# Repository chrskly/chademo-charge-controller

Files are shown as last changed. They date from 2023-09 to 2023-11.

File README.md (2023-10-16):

# CHAdeMO Implementation

This repo contains a car-side implementation of the CHAdeMO EV charging
standard including both the hardware and firmware.

## Features

* Supports CHAdeMO protocols v0.9, v1.0, and v2.0.
* Automatic sleep, wake on plug insertion.
* Separate manual wake button option.

## Chademo Plug Pinout

 1. Ground
 2. CP : evse => car, IN1, contactor +ve signal, goes high when active, sensed by 'f'
 3. nc
 4. CP3 : car => evse, OUT1, charge enable, sensed by 'k'
 5. HV-
 6. HV+
 7. CS : connection check, goes low when plug inserted, sensed by 'h'
 8. CAN H
 9. CAN L
10. CP2 : evse => car, IN2, contactor -ve signal, goes low when active, sensed by 'g'

OUT2, contactor override, pull low to allow CP2 signal through

## Charging start sequence

1. Car pulls CP high (12V) through R3 (1kΩ) when plug is inserted
2. User presses start button on station
3. Station pulls CP high (IN1), d1 closes, +ve contactor closes
4. Car and station start sending CAN messages
5. Car and station check each others params for compatability
6. Car pulls CP3 low and sets CAN vehicleChargingEnabled flag to true to
   indicate it is ready to go ahead with charging
7. Station locks plug to vehicle
8. Station performs insulation test
9. Station pulls CP2 low (IN2), d2 closes, -v3 contactor closes
10. Car ramps up current request. Energy transfer begins.

## Charging stop sequence

1. Car stops pulling CP3 low and sets CAN vehicleChargingEnabled to false.
2. Station deactivates CP and CP2
3. Station unlocks plug

## Questions

- [ ] When to use vehicleChargingEnabled and when to use vehicleRequestingStop?

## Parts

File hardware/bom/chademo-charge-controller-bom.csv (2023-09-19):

Comment | Designator | Footprint | LCSC
TPS62160DGKR | IC1 | MSOP-8 | C60726
SS54 | D1 | SMB(DO-214AA) | C880743
10uF | C1,C5,C6,C7, | 0805_C | C15850
2.2uH | L1 | IND-SMD | C92941
100kΩ | R1 | 0805_R | C149504
220kΩ | R2 | 0805_R | C17539
47kΩ | R3 | 0805_R | C17713
22uF | C4 | 0805_C | C2835558
0.1uF | C2,C3 | 0805_C | C49678
MCP2515-I/ST | IC2,IC4 | TSSOP-20 | C15193
SN65HVD230 | IC3,IC5 | SOIC-8 | C12084
120Ω | R12,R13 | 0805_R | C17437
560Ω | R17,R18,R19 | 0805_R | C28636
10Ω | R5,R8,R9,R11,R15,R20,R23 | 0805_R | C17415
1.6kΩ | R4,R10,R16,R21 | 0805_R | C2930156
led | D2,D3,D4,D5,D6,D7,D8 | 0805 | C434432
200Ω | R6 | 0805_R | C17540
1kΩ | R14 | 0805_R | C17513
100Ω | R7,R22 | 0805_R | C17408
PC817 | U2,U3,U4,U5,U6,U7 | DIP-4 | C3025067
NCV8402ASTT1G | IC6 | SOT223 | C77755

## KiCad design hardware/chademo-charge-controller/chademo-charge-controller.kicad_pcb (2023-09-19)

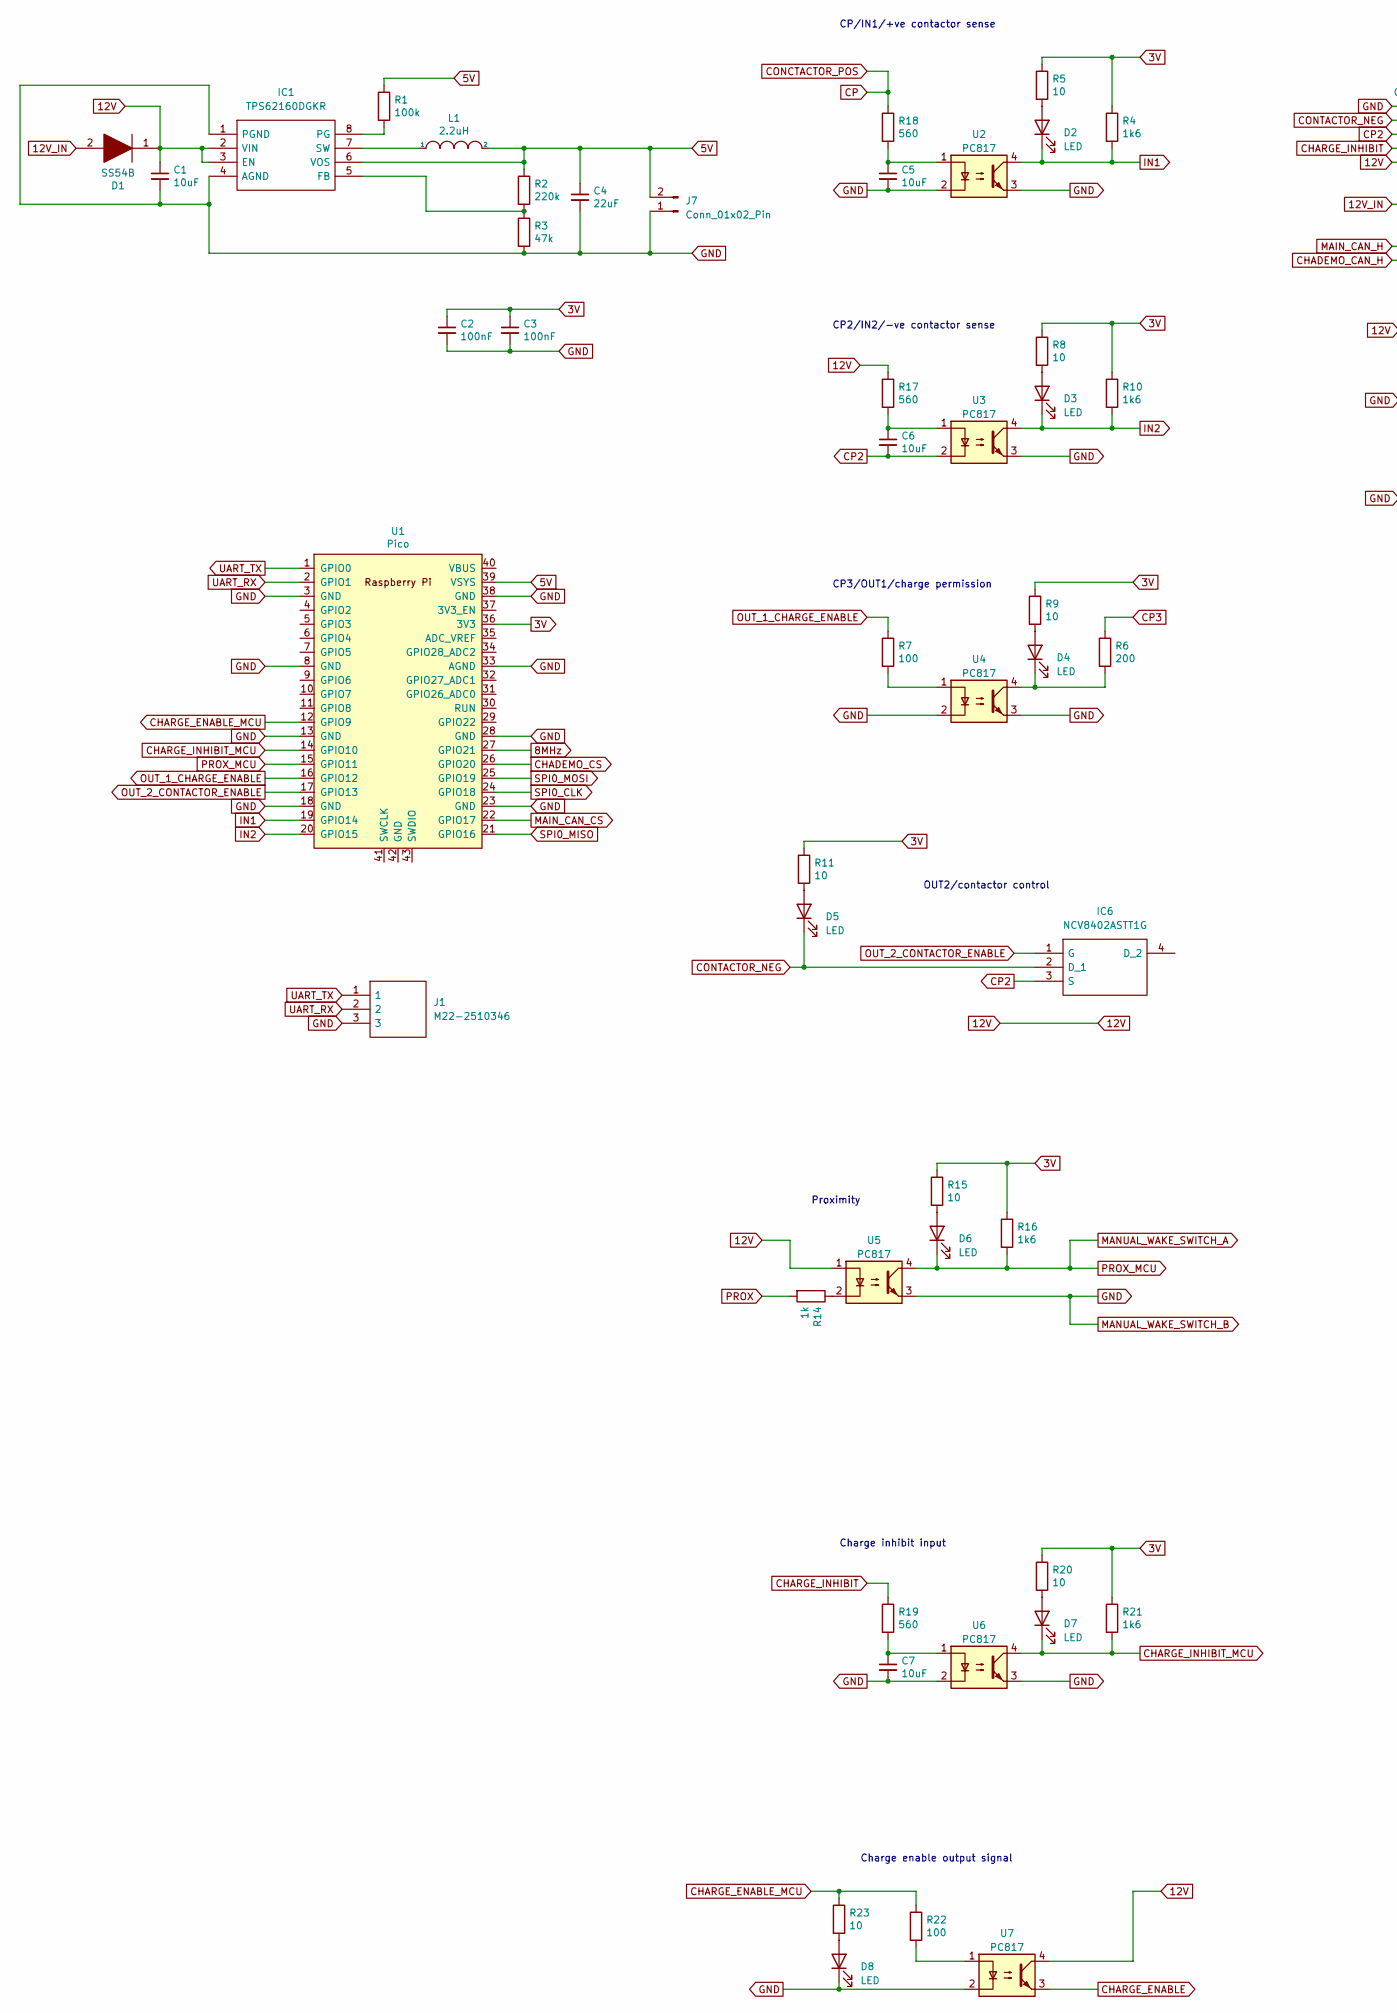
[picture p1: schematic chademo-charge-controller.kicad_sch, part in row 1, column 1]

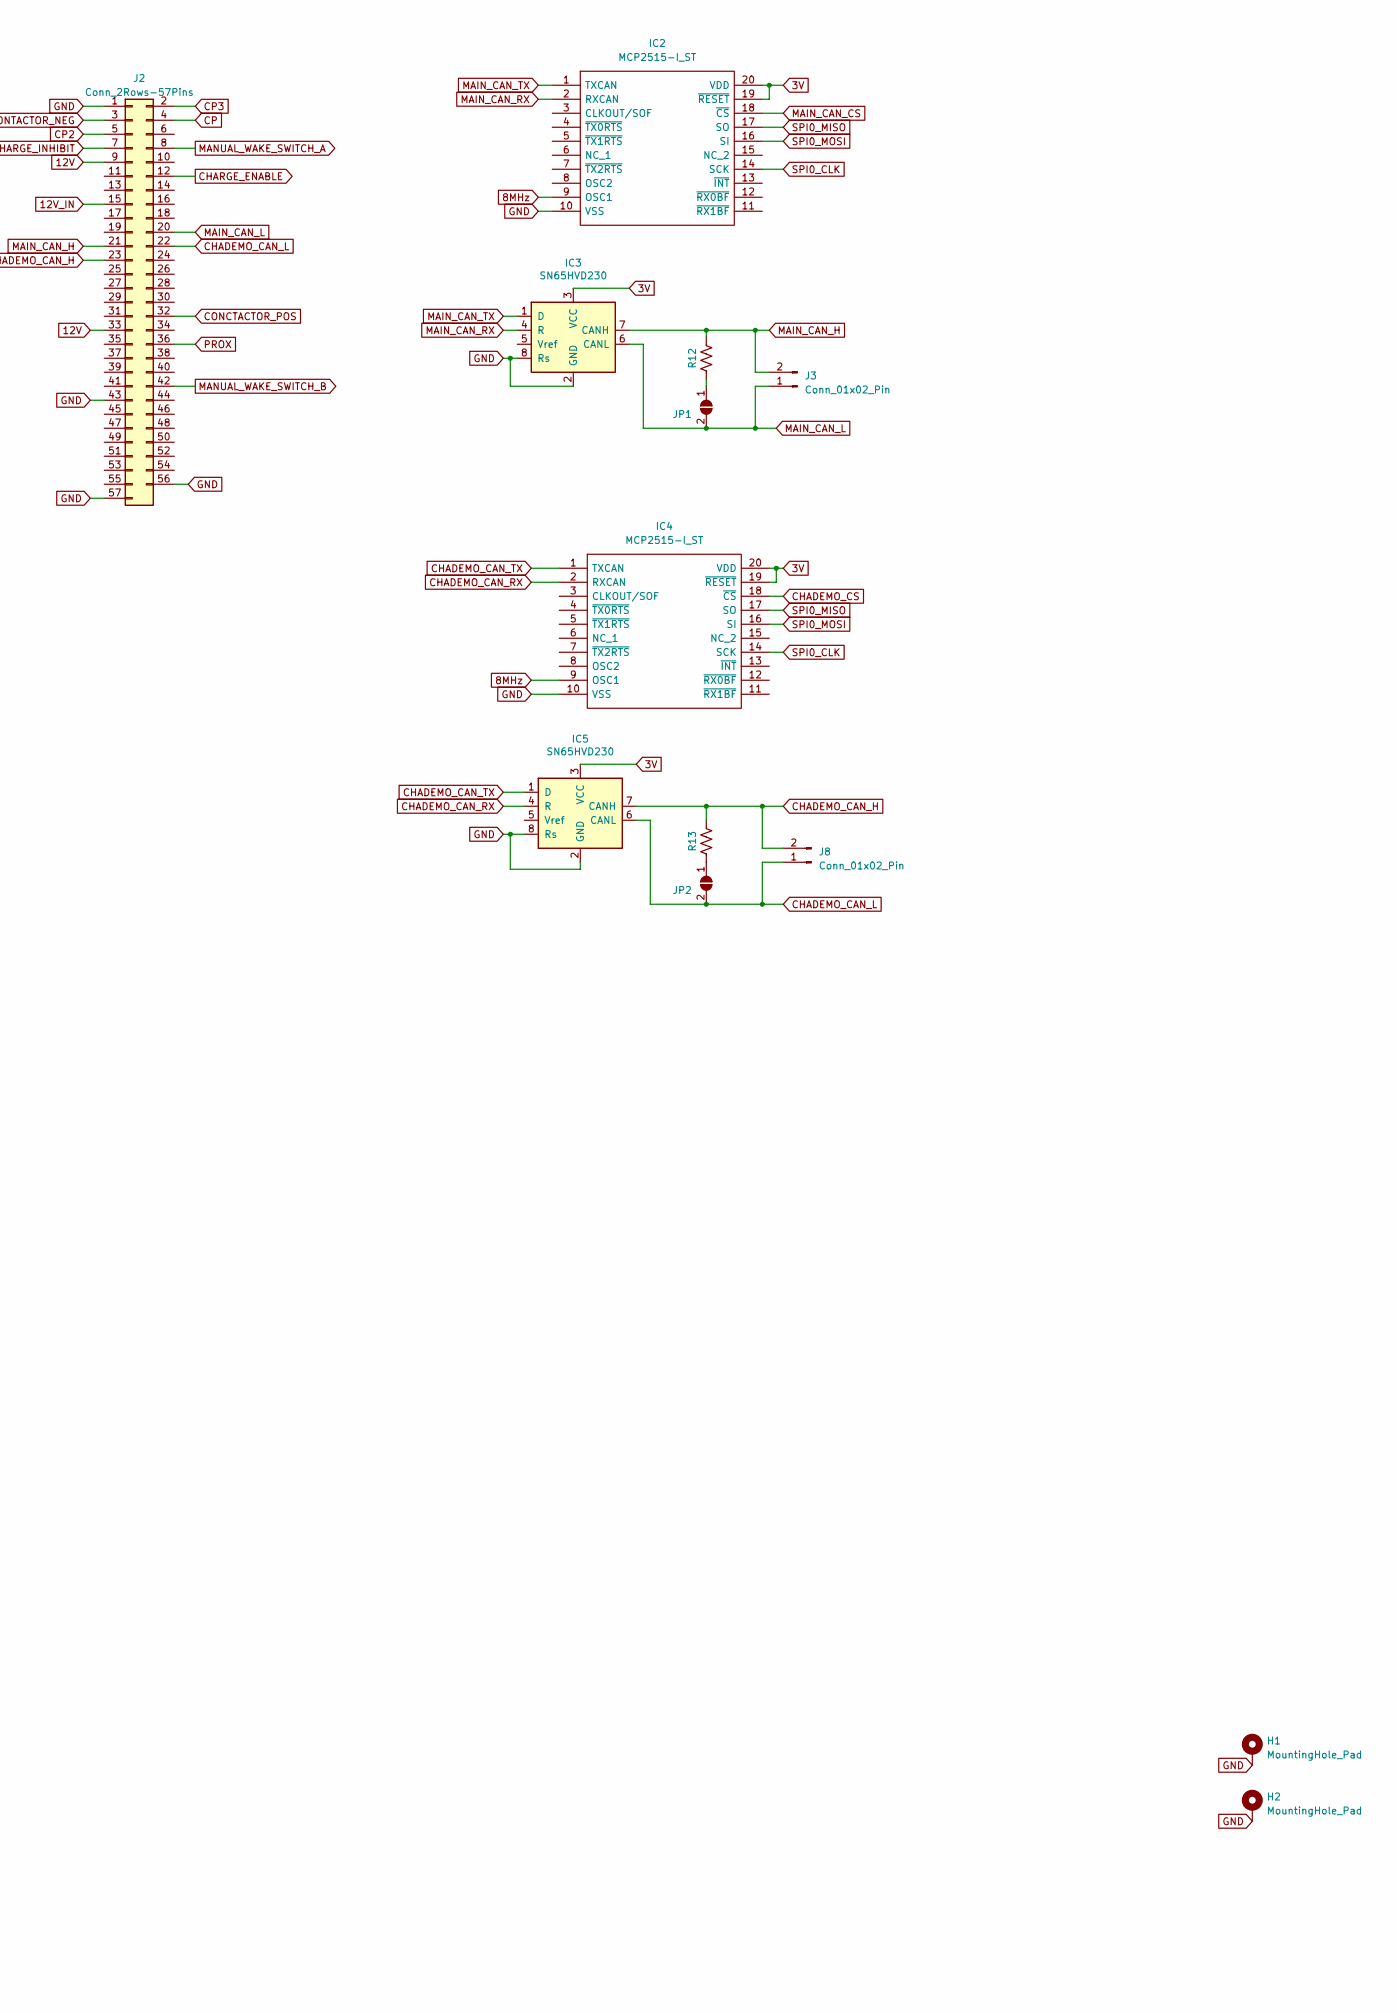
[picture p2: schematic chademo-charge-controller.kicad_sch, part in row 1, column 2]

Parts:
C1, C5, C6, C7: 10uF; C_0603_1608Metric
C2, C3: 100nF; C_0603_1608Metric
C4: 22uF; C_0805_2012Metric
D1: SS54B; DIOM5336X244N; Manufacturer_Part_Number SS54B
D2, D3, D4, D5, D6, D7, D8: LED; LED_0805_2012Metric
H1, H2: MountingHole_Pad; MountingHole_3.2mm_M3_DIN965_Pad
IC1: TPS62160DGKR; SOP65P490X110-8N; Manufacturer_Part_Number TPS62160DGKR; Mouser Part Number 595-TPS62160DGKR
IC2, IC4: MCP2515-I_ST; SOP65P640X120-20N; Manufacturer_Part_Number MCP2515-I/ST
IC3, IC5: SN65HVD230; SOIC-8_3.9x4.9mm_P1.27mm
IC6: NCV8402ASTT1G; SOT230P700X175-4N; Manufacturer_Part_Number NCV8402ASTT1G; Mouser Part Number 863-NCV8402ASTT1G
J1: M22-2510346; PinHeader_1x03_P2.54mm_Horizontal; Manufacturer_Part_Number M22-2510346; Mouser Part Number 855-M22-2510346
J2: Conn_2Rows-57Pins; delphi56
J3, J7, J8: Conn_01x02_Pin; PinHeader_1x02_P2.54mm_Vertical
JP1, JP2: SolderJumper_2_Open; SolderJumper-2_P1.3mm_Open_Pad1.0x1.5mm
L1: 2.2uH; NR6028T220M
R1: 100k; R_0805_2012Metric
R2: 220k; R_0805_2012Metric
R3: 47k; R_0805_2012Metric
R4, R10, R16, R21: 1k6; R_0805_2012Metric
R5, R8, R9, R11, R15, R20, R23: 10; R_0805_2012Metric
R6: 200; R_0805_2012Metric
R7, R22: 100; R_0805_2012Metric
R12, R13: 120; R_0805_2012Metric
R14: 1k; R_0805_2012Metric
R17, R18, R19: 560; R_0805_2012Metric
U1: Pico; RPi_Pico_SMD_TH
U2, U3, U4, U5, U6, U7: PC817; DIP-4_W7.62mm

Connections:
3V: C2.1, C3.1, IC2.19 (~RESET), IC2.20 (VDD), IC3.3 (VCC), IC4.19 (~RESET), IC4.20 (VDD), IC5.3 (VCC), R4.1, R5.1, R8.1, R9.1, R10.1, R11.1, R15.1, R16.1, R20.1, R21.1, U1.36 (3V3)
5V: C4.1, IC1.6 (VOS), J7.2, L1.2, R1.1, R2.1, U1.39 (VSYS)
8MHz: IC2.9 (OSC1), IC4.9 (OSC1), U1.27 (GPIO21)
12V: C1.1, D1.1, IC1.2 (VIN), IC1.3 (EN), J2.9, J2.33, R17.1, U5.1, U7.4
12V_IN: D1.2, J2.15
CHADEMO_CAN_H: IC5.7 (CANH), J2.23, J8.2, R13.1
CHADEMO_CAN_L: IC5.6 (CANL), J2.22, J8.1, JP2.2 (B)
CHADEMO_CAN_RX: IC4.2 (RXCAN), IC5.4 (R)
CHADEMO_CAN_TX: IC4.1 (TXCAN), IC5.1 (D)
CHADEMO_CS: IC4.18 (~CS), U1.26 (GPIO20)
CHARGE_ENABLE: J2.12, U7.3
CHARGE_ENABLE_MCU: R22.1, R23.1, U1.12 (GPIO9)
CHARGE_INHIBIT: J2.7, R19.1
CHARGE_INHIBIT_MCU: D7.1 (K), R21.2, U1.14 (GPIO10), U6.4
CONCTACTOR_POS: J2.4, J2.32, R18.1
CONTACTOR_NEG: D5.1 (K), IC6.2 (D_1), J2.3
CP2: C6.2, IC6.3 (S), J2.5, U3.2
CP3: J2.2, R6.1
GND: C1.2, C2.2, C3.2, C4.2, C5.2, C7.2, D8.1 (K), H1.1, H2.1, IC1.1 (PGND), IC1.4 (AGND), IC2.10 (VSS), IC3.2 (GND), IC3.8 (Rs), IC4.10 (VSS), IC5.2 (GND), IC5.8 (Rs), J1.3, J2.1, J2.42, J2.43, J2.56, J2.57, J7.1, R3.2, U1.3 (GND), U1.8 (GND), U1.13 (GND), U1.18 (GND), U1.23 (GND), U1.28 (GND), U1.33 (AGND), U1.38 (GND), U2.2, U2.3, U3.3, U4.2, U4.3, U5.3, U6.2, U6.3, U7.2
IN1: D2.1 (K), R4.2, U1.19 (GPIO14), U2.4
IN2: D3.1 (K), R10.2, U1.20 (GPIO15), U3.4
MAIN_CAN_CS: IC2.18 (~CS), U1.22 (GPIO17)
MAIN_CAN_H: IC3.7 (CANH), J2.21, J3.2, R12.1
MAIN_CAN_L: IC3.6 (CANL), J2.20, J3.1, JP1.2 (B)
MAIN_CAN_RX: IC2.2 (RXCAN), IC3.4 (R)
MAIN_CAN_TX: IC2.1 (TXCAN), IC3.1 (D)
MANUAL_WAKE_SWITCH_A: D6.1 (K), J2.8, R16.2, U1.15 (GPIO11), U5.4
unnamed: C5.1, R18.2, U2.1
unnamed: C6.1, R17.2, U3.1
unnamed: C7.1, R19.2, U6.1
unnamed: D2.2 (A), R5.2
unnamed: D3.2 (A), R8.2
unnamed: D4.2 (A), R9.2
unnamed: D4.1 (K), R6.2, U4.4
unnamed: D5.2 (A), R11.2
unnamed: D6.2 (A), R15.2
unnamed: D7.2 (A), R20.2
unnamed: D8.2 (A), R23.2
unnamed: IC1.5 (FB), R2.2, R3.1
unnamed: IC1.8 (PG), R1.2
unnamed: IC1.7 (SW), L1.1
unnamed: JP1.1 (A), R12.2
unnamed: JP2.1 (A), R13.2
unnamed: R7.2, U4.1
unnamed: R14.1, U5.2
unnamed: R22.2, U7.1
OUT_1_CHARGE_ENABLE: R7.1, U1.16 (GPIO12)
OUT_2_CONTACTOR_ENABLE: IC6.1 (G), U1.17 (GPIO13)
PROX: J2.36, R14.2
SPI0_CLK: IC2.14 (SCK), IC4.14 (SCK), U1.24 (GPIO18)
SPI0_MISO: IC2.17 (SO), IC4.17 (SO), U1.21 (GPIO16)
SPI0_MOSI: IC2.16 (SI), IC4.16 (SI), U1.25 (GPIO19)
UART_RX: J1.2, U1.2 (GPIO1)
UART_TX: J1.1, U1.1 (GPIO0)

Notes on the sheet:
CP/IN1/+ve contactor sense
OUT2/contactor control
CP3/OUT1/charge permission
CP2/IN2/-ve contactor sense
Charge inhibit input
Charge enable output signal
Proximity

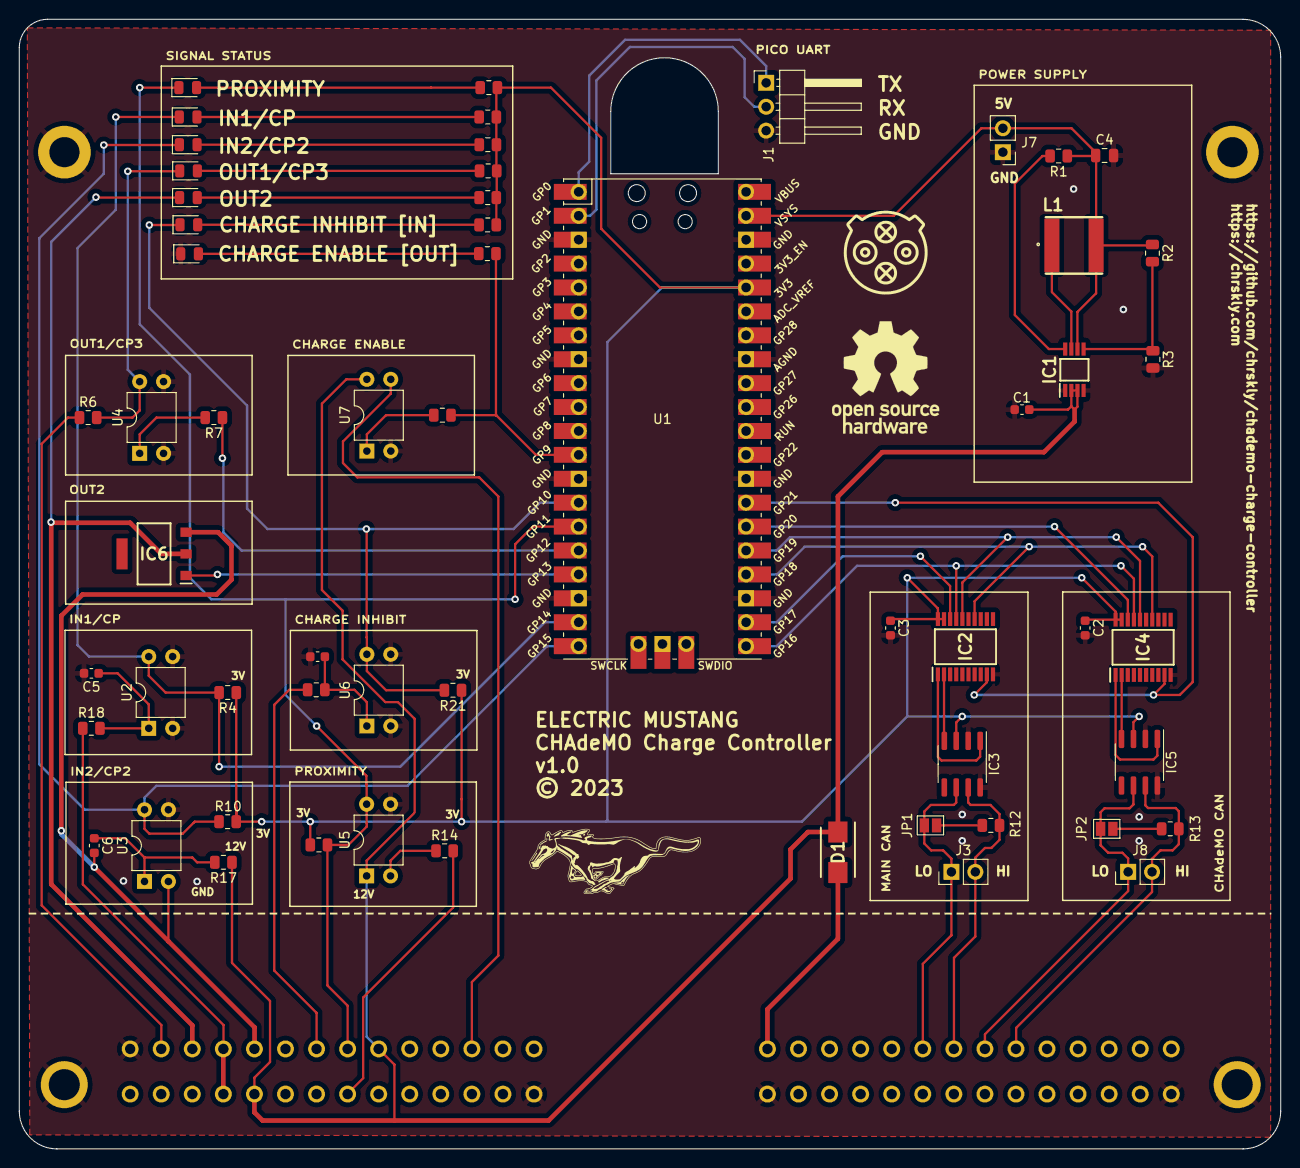
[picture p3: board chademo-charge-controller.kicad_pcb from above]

Board: 2 copper layers, 134.0 x 120.0 mm, 61 parts (0 on the bottom side), 54 nets.

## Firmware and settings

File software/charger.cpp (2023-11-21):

/*
 * This file is part of the ev mustang charge controller project.
 *
 * Copyright (C) 2022 Christian Kelly <chrskly@chrskly.com>
 *
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
 * You should have received a copy of the GNU General Public License
 * along with this program.  If not, see <http://www.gnu.org/licenses/>.
 */

using namespace std;

#include <string.h>
#include <time.h>
#include <stdio.h>
#include "pico/stdlib.h"
#include "hardware/spi.h"
#include "hardware/uart.h"
#include "hardware/gpio.h"
#include "hardware/clocks.h"
#include "pico/cyw43_arch.h"
#include "pico/stdlib.h"
#include "lwip/pbuf.h"
#include "lwip/tcp.h"
#include "hardware/watchdog.h"

extern "C" {
    #include "led.h"
    #include "battery.h"
    #include "settings.h"
    #include "chademo.h"
    #include "statemachine.h"
    #include "dhcpserver.h"
    #include "dnsserver.h"
    #include "wifi.h"
}

#include "mcp2515/mcp2515.h"
#include "comms.h"
#include "chademocomms.h"

#include "charger.h"
#include "types.h"



MCP2515 mainCAN(SPI_PORT, MAIN_CAN_CS, SPI_MISO, SPI_MOSI, SPI_CLK, 500000);
MCP2515 chademoCAN(SPI_PORT, CHADEMO_CAN_CS, SPI_MISO, SPI_MOSI, SPI_CLK, 500000);


Charger charger;
State state;
Station station;
BMS bms;
Battery battery;
StatusLED led;
Chademo chademo;


// Watchdog

struct repeating_timer watchdogKeepaliveTimer;

bool watchdog_keepalive(struct repeating_timer *t) {
    watchdog_update();
    return true;
}

void enable_watchdog_keepalive() {
    add_repeating_timer_ms(5000, watchdog_keepalive, NULL, &watchdogKeepaliveTimer);
}


int main() {
    stdio_init_all();

    set_sys_clock_khz(80000, true);

    // set up the serial port
    uart_init(UART_ID, BAUD_RATE);
    gpio_set_function(UART_TX_PIN, GPIO_FUNC_UART);
    gpio_set_function(UART_RX_PIN, GPIO_FUNC_UART);

    printf("Charger starting up ...\n");

    chademo_reinitialise();

    // Set up blinky LED
    gpio_init(PICO_DEFAULT_LED_PIN);
    gpio_set_dir(PICO_DEFAULT_LED_PIN, GPIO_OUT);
    led_set_mode(STANDBY);
    enable_led_blink();

    // 8MHz clock for CAN oscillator
    clock_gpio_init(CAN_CLK_PIN, CLOCKS_CLK_GPOUT0_CTRL_AUXSRC_VALUE_CLK_SYS, 10);

    printf("Setting up main CAN port (BITRATE:%d:%d)\n", CAN_500KBPS, MCP_8MHZ);
    mainCAN.reset();
    mainCAN.setBitrate(CAN_500KBPS, MCP_8MHZ);
    mainCAN.setNormalMode();
    printf("Enabling handling of inbound CAN messages on main bus\n");
    enable_handle_main_CAN_messages();

    enable_bms_liveness_check();

    printf("Setting up Chademo CAN port (BITRATE:%d:%d)\n", CAN_500KBPS, MCP_8MHZ);
    chademoCAN.reset();
    chademoCAN.setBitrate(CAN_500KBPS, MCP_8MHZ);
    chademoCAN.setNormalMode();
    printf("Enabling handling of inbound CAN messages on chademo bus\n");
    enable_handle_chademo_CAN_messages();

    printf("Starting web server\n");
    TCP_SERVER_T *tcpState = new TCP_SERVER_T;

    if (cyw43_arch_init()) {
        printf("failed to initialise\n");
        return 1;
    }

    const char *ap_name = "picow_test";
    const char *password = "password";

    cyw43_arch_enable_ap_mode(ap_name, password, CYW43_AUTH_WPA2_AES_PSK);

    ip4_addr_t mask;
    IP4_ADDR(ip_2_ip4(&tcpState->gw), 192, 168, 4, 1);
    IP4_ADDR(ip_2_ip4(&mask), 255, 255, 255, 0);

    dhcp_server_t dhcp_server;
    dhcp_server_init(&dhcp_server, &tcpState->gw, &mask);

    if (!tcp_server_open(tcpState, ap_name)) {
        printf("failed to open server\n");
        return 1;
    }

    tcpState->complete = false;

    while(!tcpState->complete) {
        cyw43_arch_poll();
        cyw43_arch_wait_for_work_until(make_timeout_time_ms(1000));
    }

    return 0;
}

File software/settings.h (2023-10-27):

/*
 * This file is part of the ev mustang charge controller project.
 *
 * Copyright (C) 2022 Christian Kelly <chrskly@chrskly.com>
 *
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
 * You should have received a copy of the GNU General Public License
 * along with this program.  If not, see <http://www.gnu.org/licenses/>.
 */

#ifndef SETTINGS_H
#define SETTINGS_H

#define VERSION 1.0

// Serial port
#define UART_ID      uart0
#define BAUD_RATE   115200
#define UART_TX_PIN      0 // pin 1
#define UART_RX_PIN      1 // pin 2

// SPI
#define SPI_PORT      spi0
#define SPI_MISO        16 // pin 21
#define SPI_CLK         18 // pin 24
#define SPI_MOSI        19 // pin 25
#define CAN_CLK_PIN     21 // pin 27
#define MAIN_CAN_CS     17 // pin 22
#define CHADEMO_CAN_CS  20 // pin 26

// Inputs
#define PROX_PIN 11
#define CHADEMO_IN1_PIN 14  // pin 19, CP  - contactor +ve, (sensed by 'f'), d1 enable signal, chademo plug pin 2
#define CHADEMO_IN2_PIN 15  // pin 20, CP2 - contactor -ve, (sensed by 'g'), d2 enable signal, chademo plug pin 10
#define CHADEMO_CS_PIN 20   // pin 26, CS - pilot wire, input, (a.k.a 'h'), pilot signal, chademo plug pin 7

// Outputs
#define CHARGE_ENABLE_PIN 9     // pin 12
#define CHARGE_INHIBIT_PIN 10   // pin 14
#define CHADEMO_OUT1_PIN 12     // pin 16, CP3 - charge enable, (switched by 'k'), chademo plug pin 4
#define CHADEMO_OUT2_PIN 13     // pin 17, contactor relay control, 'e'
#define PICO_DEFAULT_LED_PIN 99 //


/*
 * General CHAdemMO settings
 */

/* Version of CHADeMO protocol that the vehicle will announce to the station
 * 0 == Before 0.9
 * 1 == v0.9 and v0.9.1
 * 2 == v1.0.0 and v1.0.1
 * 3 == v2.0.0 and v2.0.1
 */
#define CHADEMO_PROTOCOL_VERSION 1

// Messages from ChaDeMo station
#define EVSE_CAPABILITIES_MESSAGE_ID 0x108
#define EVSE_STATUS_MESSAGE_ID 0x109

// Spec says current requests from the car should only vary at a rate of +/- 20A/sec
#define CHADEMO_RAMP_RATE 20
#define CHADEMO_RAMP_INTERVAL 1000 // units = ms

// If we don't receive a CAN message from the ChaDeMo station in this number of
// seconds, then we must abort charging.
#define CHADEMO_STATION_TTL 2000 // units = ms

// This scaling factor is used to calculate max charging time from the estimated charging time
#define MAX_CHARGING_TIME_SCALING_FACTOR 1.2

/* Specify whether to use amp-hours (ah) or watt-hours (wh) to estimate how much
 * time is left to complete charging.
 */
#define CALCULATE_TIME_REMAINING_BASED_ON "ah"

/* The energy transfer stage is complete when the current drops below this value.
 */
#define TERMINATION_CURRENT 5

/* How long we wait for the contactors to open/close when we're doing weld
 * detection. If it takes longer than this, we consider the contactors welded.
 */
#define WELD_CHECK_TTL 1000 // units = ms


/*
 * General BMS settings
 */

// If we don't receive a CAN message from the BMS in this number of seconds,
// then we must abort charging.
#define BMS_TTL 5000 // units = ms

// BMS CAN message which contains max/min pack voltage, max dis/charge current
#define BMS_LIMITS_MESSAGE_ID 0x351

// BMS CAN messages which contains SoC
#define BMS_SOC_MESSAGE_ID 0x355

// BMS CAN message which contains pack voltage, current (not implemented), temp
#define BMS_STATUS_MESSAGE_ID 0x356

// BMS CAN message which contains alarms/warnings from BMS
#define BMS_ALARM_MESSAGE_ID 0x35A


/*
 * Battery settings
 */

// The SoC at which to stop fast-charging. Can be overriden via CAN msg.
#define BATTERY_FAST_CHARGE_DEFAULT_SOC_MAX 80

#define BATTERY_MAX_CURRENT 10          // fixme put in proper value
#define BATTERY_MAX_CURRENT_FAILSAFE 10 // maximum current to use if we lose communication with the BMS

// Stop charging when current drops to this level
#define TERMINATE_CHARGING_CURRENT 5

#endif

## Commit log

2023-07-19 Basic hardware layout
    [chademo-charge-controller.kicad_pcb, chademo-charge-controller.kicad_sch]
2023-07-20 pcb layout, 56pin socket
    [chademo-charge-controller.kicad_pcb, chademo-charge-controller.kicad_sch]
2023-07-28 tweaking hw
    [chademo-charge-controller.kicad_pcb, chademo-charge-controller.kicad_sch]
2023-08-06 lots of work on hardware
    [chademo-charge-controller.kicad_pcb, chademo-charge-controller.kicad_sch]
2023-09-19 I dunno ... lots
    [chademo-charge-controller-B_Cu.gbl, chademo-charge-controller-B_Mask.gbs, chademo-charge-controller-B_Paste.gbp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]
2023-10-16 Add BMS liveness check
2023-10-16 terminate current setting
2023-10-18 missing prototype
2023-10-21 Use max voltage from bms rather than hardcoded value
2023-10-21 Fixing some parts of flow
    [chademo.c]
2023-10-21 Get charge current limit straight from BMS
2023-10-23 More work on flow
2023-10-24 Implement current deviation error logic
    [chademo.c]
2023-10-27 Deal with more error states
    [chademo.c]
2024-08-03 Fix voltage graph figures
2024-08-04 Add status/history/settings subtabs to battery tab

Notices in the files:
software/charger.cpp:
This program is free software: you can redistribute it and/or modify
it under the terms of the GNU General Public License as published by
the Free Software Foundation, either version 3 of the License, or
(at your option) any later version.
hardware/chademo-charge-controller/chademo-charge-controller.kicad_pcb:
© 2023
